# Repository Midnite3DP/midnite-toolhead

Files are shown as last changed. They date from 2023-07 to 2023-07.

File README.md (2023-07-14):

# Midnite Toolhead

Inspired by the [VzBot Printed Printhead](https://github.com/VzBoT3D/Vz-Printhead-Printed) and the [EVA Carriage](https://main.eva-3d.page/), the Midnite Toolhead is designed to provide a back-attached CPAP cooling duct that is more compact and reduces the amount of Y travel lost when using the same cooling set up provided by VzBot and EVA on a Voron-style printer.



## Design
Similar to VzBot, the design relies on 4 x 30mm aluminum standoffs and a top and bottom printed piece. 

There are only 5 necessary parts: the CPAP cooling duct, the duct spacer, the bottom part cooling duct, the top carriage piece, and the bottom carriage piece.

Unlike the VzBot Printhead, the back fan duct isn't an entire assembly designed to slide up and down. This makes my design much more limited (it doesn't include a cable holder, a large sliding range of motion to support many hotends, etc) but the tradeoff is hopefully worth it. 

This is designed for a voron-style printer, only requiring a top-mounted X rail. Your front belts loop around the front aluminum standoffs and then are held in place with VzBot belt clamps.



## Compatibility
This was made with these components in mind:
- Sherpa Mini Extruder (mine is CNC but it should work exactly the same for the printed version)
- VzBot Goliath Hotend (mine is watercooled but I think the mounting holes are the same for the air-cooled version)
- CPAP Cooling (I am using the standard CPAP tubing, which comes with a rubber end that I just push onto the end of the CPAP duct)
- SHT36 CAN Board (I'm sure others will work fine but this is the one I have been using and including in my models and test builds)
- Beacon Probe (The bottom fan duct has mounting holes for it, but this has not been tested yet, so there may be conflicts with the no-metal zone)
- Any Voron gantry, as long as you flip your X assembly (extrusion & XY joints) because that allows you to install a top-mounted rail. Flipping your X assembly shouldn't change anything (belt pathing, performance, etc), it just means your Y linear rails are also on top.
- If you have backers, they just go on the opposite side your rails are installed on the extrusions, just make sure your backer screws are flush - there's only 2mm of extra clearance to account for backers.
- You will need to run some tests to test the X and Y endstops. Currently this isn't a step I've gotten to in the development, so you'll need to either find your own solution for this, suggest one in an issue, or wait for (if/when) there is an update here.

## Bill of Materials
- 4 x 5x30mm Aluminum Standoffs (for carriage assembly)
- 8 x 16mm M3 Flat Head Countersunk Screws (for top & bottom carriage plates)
- 4 x 8mm M3 Flat Head Countersunk Screws (for attaching top carriage plate to MGN12H linear rail carriage)
- 2 x 6mm M3 Button Head Screws (for attaching the endstop piece to the top of the rail)
- 2 x 8mm M3 Button Head Screws (for attaching CPAP fan duct on the back, thru duct spacer, to bottom cooling duct)
- 2 x 10mm M3 Button Head Screws (for attaching Sherpa Mini Extruder to top carriage plate)
- 2 x 18mm M3 Button Head Screws (for attaching the bottom cooling duct, thru carriage spacer, to bottom carriage plate) [This is sort of optional but adds a lot of strength and prevents the CPAP fan duct from snapping off at the 90 degree bend]
- 6 x 5mm M3 Heatset Inserts (2 for the carriage top plate for attaching Sherpa Mini, 2 for bottom fan duct for attaching CPAP fan duct thru duct spacer)

## Printability
The CPAP fan duct is not easy to print. The only orientation I've found is shown in the image below. My settings are stock from Andrew Ellis's print guide. I have a 0.6mm nozzle, printing Sparta ABS+, at 240C, with Supports on build plate and Brim turned on.



## Assembly
Install it whatever way makes sense to you. Note that you should read through the steps and do things differently depending on your setup. For example, you might want 

Here's how I do it:
1. Put the CPAP fan duct and the bottom carriage piece together, then put the back 2 aluminum standoffs thru the CPAP fan duct holes and into the bottom carriage piece.
2. Push the CPAP fan duct all the way down (while it's freely sliding up and down on the aluminum standoffs) to make room, then put the screws into the back 2 aluminum standoffs thru the bottom carriage piece. Try to not snap off the CPAP fan duct's mounting holes.
3. Put the front 2 aluminum standoffs into the bottom carriage piece, then screw them in.
4. At this point, if your X assembly (extrusion + linear rail) is already installed, you can do the next step around your extrusion. Meaning, when you put the top carriage piece down onto the aluminum standoffs that are in the bottom piece, you're doing it directly on your X rail.
5. Put the top carriage piece down onto the aluminum standoffs carefully and as straight as possible so you don't snap the plastic around the standoffs. Screw the aluminum standoffs in.
6. Install the heatset inserts on the top and bottom carriage pieces (this can be done at any step but I do it on this step so if I broke anything, I don't have to salvage heatset inserts from broken parts or leave them in the broken parts and waste them)
7. Install the heatset inserts on the bottom fan duct. Put screws through the holes in the bottom fan duct up thru the carriage spacers, ready for the next step
8. Screw thru the CPAP fan duct mount holes, thru the fan spacer (make sure the flat side of the fan spacer is touching the bottom fan duct), into the bottom fan duct.
9. Screw from the bottom the bottom fan duct thru the carriage spacers, into the bottom carriage.
10. Install the whole assembly onto your X rail if you haven't done so already, assuming your X assembly isn't pre-installed and set up. If your X assembly isn't in the printer, you can easily slide on the entire built assembly onto it, then screw it into the linear rail.
11. Install your Hotend and Extruder. This can technically be done in any order, but note that the motor on the Sherpa Mini extruder will make it difficult/impossible to access the screws for installing the toolhead onto a linear rail. The Hotend screws are also impossible to access with the extruder installed.

These instructions are far from perfect. I recommend just putting the whole thing together outside the printer, so you understand how it goes together, then take the top off and install it onto the printer the way that works for you.

## NOTE
This is a work in progress that may or may not get updates in the future. There are **many** problems with this project. Print/use at your own risks. I have put in enough work to get it printable with my machine and my hotend, extruder, and other personal needs/requirements. If you have requests, you're welcome to submit a GitHub issue or make the change yourself using the CAD file and submit a Pull Request.

## Goals
- There is currently +/- 2mm of room to slide the CPAP fan duct up and down, with the opportunity to make this 4-6mm if future changes are made to the design to make the mounting geometry smaller or make the entire toolhead taller. The Rapido UHF is about 6/7mm shorter than the Goliath watercooled Hotend, so the goal here might be to increase the sliding up/down range up to 8-10mm.
- The CPAP fanduct probably needs to be redesigned so it has thicker walls and isn't as easy to break, as well as (somehow) changing the design so that it is easier to reliably print without a tuned printer.
- The top plate design makes it so that, in theory, adding support for more extruder mounting patterns should be relatively easy. There might also be an opportunity to have a semi-universal plate that has many mounting holes designed for many extruders, rather than making one plate per extruder.

## Gallery











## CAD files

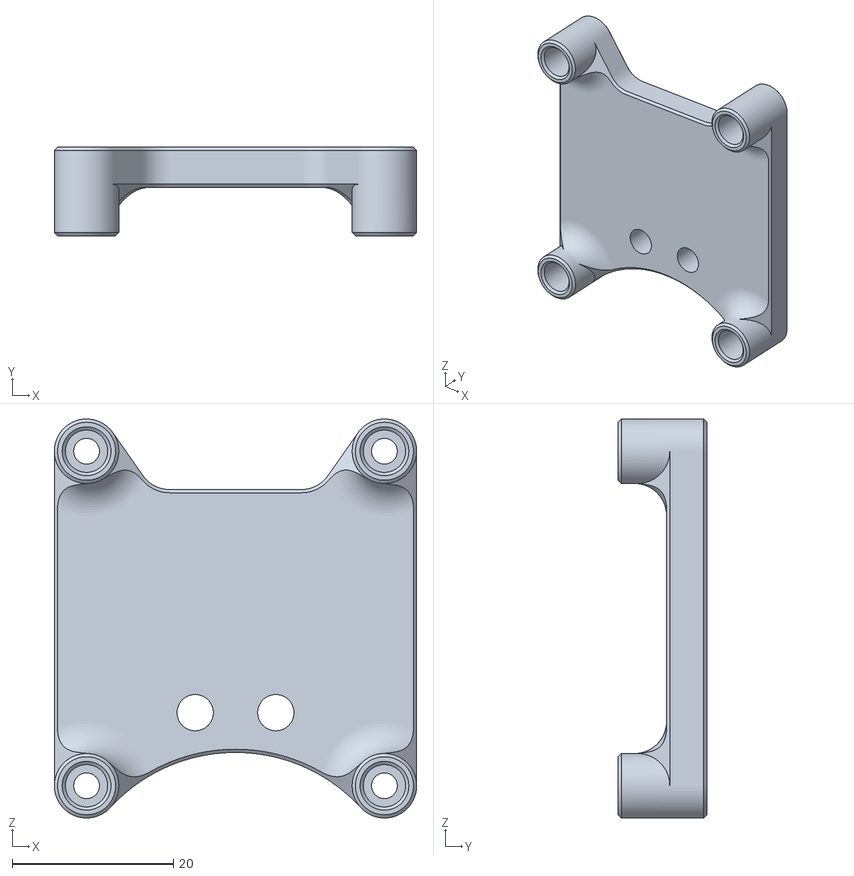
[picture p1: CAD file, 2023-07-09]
STL/Carriage_Bottom.stl
44.9 x 11.0 x 49.5

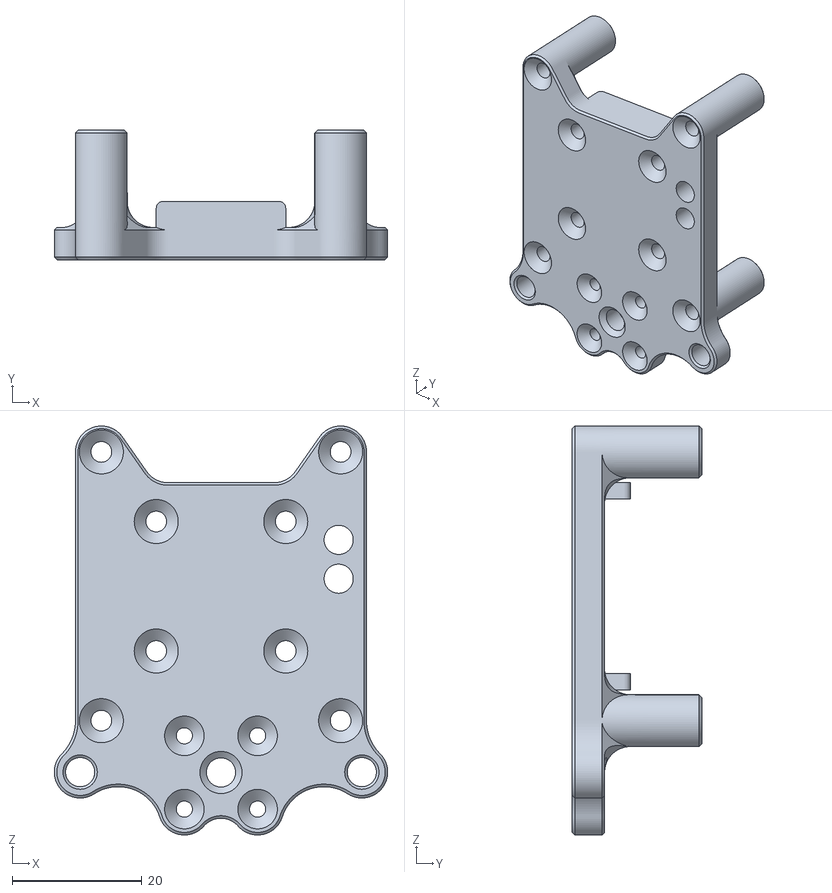
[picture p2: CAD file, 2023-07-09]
STL/Carriage_Top.stl
51.5 x 20.0 x 63.2

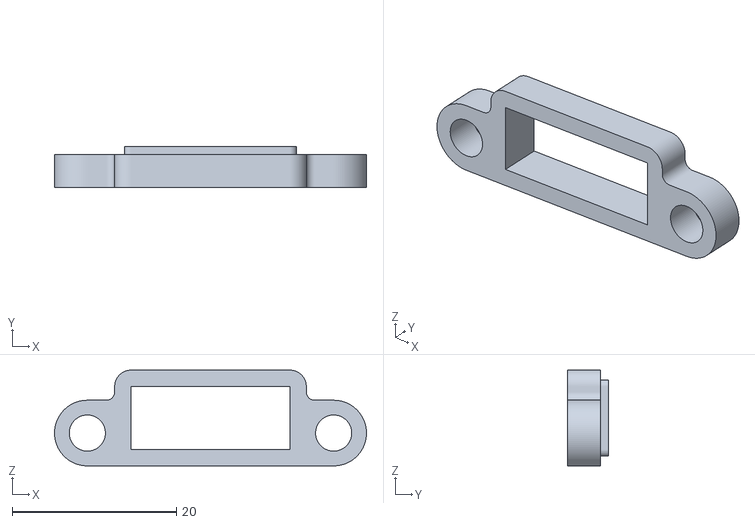
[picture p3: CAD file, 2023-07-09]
STL/Duct_Spacer.stl
38.0 x 5.00 x 11.7

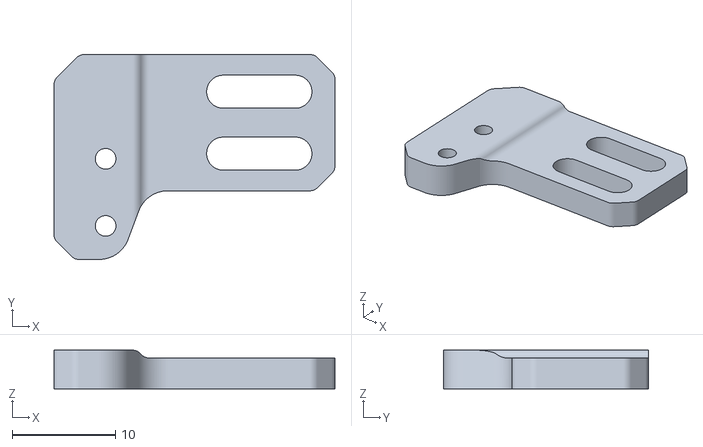
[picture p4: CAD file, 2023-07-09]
STL/Endstop_Holder.stl
27.2 x 19.8 x 3.75

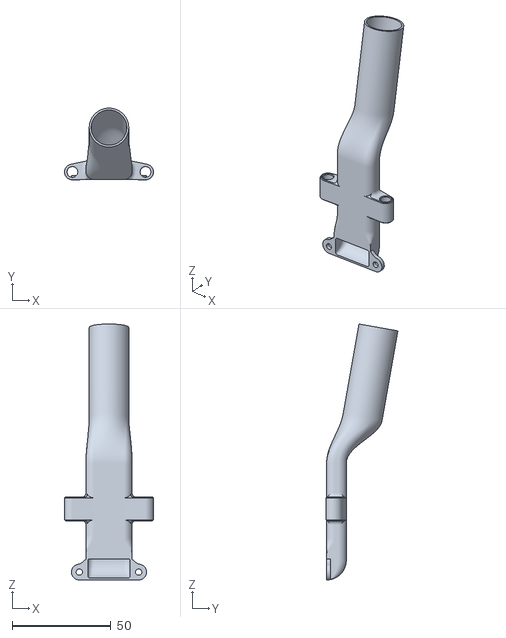
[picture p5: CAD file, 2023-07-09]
STL/CPAP_Duct.stl
44.9 x 36.3 x 129.4

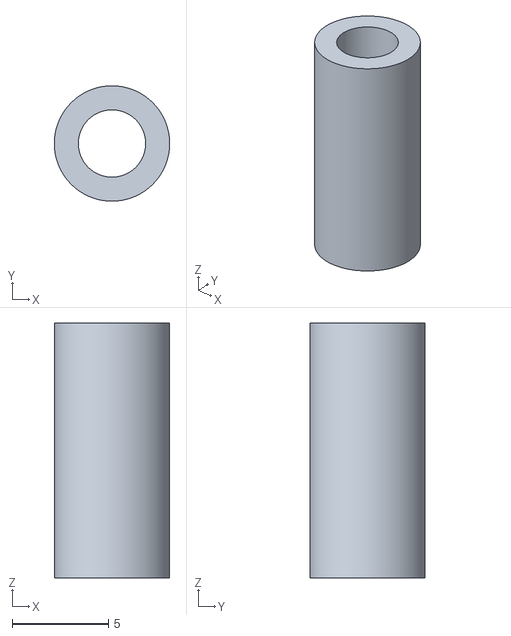
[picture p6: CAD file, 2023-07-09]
STL/Carriage_Spacer_x2.stl
6.00 x 6.00 x 13.3
